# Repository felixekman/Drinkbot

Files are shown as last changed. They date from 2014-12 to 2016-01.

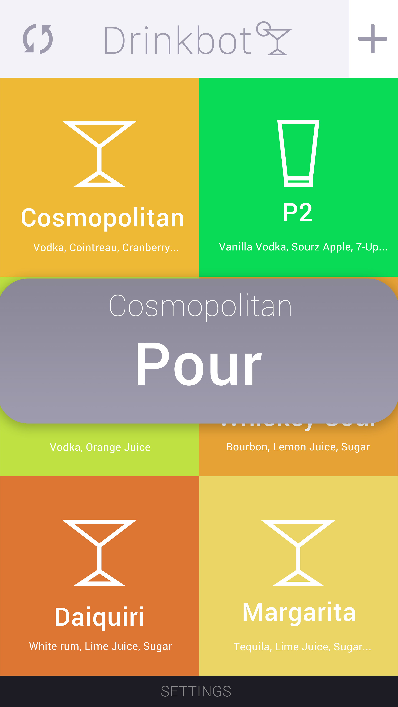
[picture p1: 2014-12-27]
AppDevelopment/AppGUI-Order.jpg

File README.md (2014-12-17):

Drinkbot
========

An attempt at controlling a bunch of peristaltic pumps

I have ordered 8 Peristaltic Pumps. 12VDC 200-300mA
  https://www.adafruit.com/products/1150

I hope to drive them via a Raspberry Pi Model B and a Spark core.
I want to be able to control the pumps individually with Mosfets for ON/OFF operation (Possibly via PWM) from the GPIO pins on the Raspberry Pi. I hope to connect the pumps via RJ45 connectors for easy connect and disconnect. I want to drive the entire system from a single 12V power supply.
My current plan is to build my own PCB (first time ever so I need a little help) using these components and ordering the PCB from OSHPark.

Components for the build:

1 pcs Raspberry Pi Model B

1 pcs Spark Core http://spark.io

8 pcs Peristaltic Pumps. 12VDC 200-300mA (https://www.adafruit.com/products/1150)

8 pcs RJ45 8-Pin connectors (https://www.sparkfun.com/products/643)

8 pcs N-Channel MOSFET 60V 30A FQP30N06L (https://www.sparkfun.com/products/10213)

8 pcs 10k Ohm 1/4th W Resistors (https://www.sparkfun.com/products/8374)

8 pcs 1N4007 Diode MIC DO-41 1A 1000V Rectifier Diode

1 pcs Voltage Regulator - 5V L7805 (https://www.sparkfun.com/products/107)

1 pcs Raspberry Pi - GPIO Shrouded Header (2x13)

This project is released under Open Source Hardware (OSHW) licence and the coming software is released under a OSI-approved open source license!

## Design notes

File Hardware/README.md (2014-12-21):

Drinkbot
========

Version 1 of Drinkbot Hardware
Schematics and Layout in Eagle CAD

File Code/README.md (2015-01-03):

Drinkbot
========

## State Machine
```
                   BOOTING
                      |
                      v
   (collect data) LISTENING <-+
        API called? Y |       |
                      v       |
                    START     |
                      |       | finished? Y
                      v       |
              +--> PUMPING    |
  finished? N |       |       |
              +-------+-------+
                      |
                      v
                     end (never reach here)
```

## APIs
```
[librae@centos build]$ spark list
Checking with the cloud...
Retrieving cores... (this might take a few seconds)
core-librae (111111111111111111111111) is online
  Variables:
    temperature (double)
    alcohol1 (double)
    alcohol2 (double)
  Functions:
    int setpumps(String args)
    int debug(String args)
```

### Variables
```
$ spark get DrinkbotPrototype temperature
1454
```
or
```
$ curl https://api.spark.io/v1/devices/111111111111111111111111/temperature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

{
  "cmd": "VarReturn",
  "name": "temperature",
  "result": 1446,
  "coreInfo": {
    "last_app": "",
    "last_heard": "2015-01-03T16:27:09.022Z",
    "connected": true,
    "deviceID": "111111111111111111111111"
  }
}
```

### Functions

```
$ spark call DrinkbotPrototype setpumps "P0:10;P1:00;P2:20;P3:05;P4:07;P5:15;P6:00;P7:10"
0
```
or
```
$ curl https://api.spark.io/v1/devices/111111111111111111111111/setpumps \
	-d access_token=ffffffffffffffffffffffffffffffffffffffff \
	-d "args=P0:03;P1:03;P2:10;P3:12;P4:01;P5:02;P6:04;P7:00"

{
  "id": "111111111111111111111111",
  "name": "core-librae",
  "last_app": null,
  "connected": true,
  "return_value": 0
}
```

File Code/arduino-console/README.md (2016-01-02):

# arduino-console
A simple portable console module for Arduino.<br>
Originally ported from Ousia console. http://ousia.accrete.org/

## Features
* Easy for adding new commands
* Arguments passing through
* Simply extendable

## Running Demo
```
console starts...
Please press ENTER to activate it.

$
$ ?
available commands:
	help
	?
	debug
```
```
$ who
who: command not found
```
```
$ debug param1 param2
argv[1]: param1
argv[2]: param2
argc: 3
cmd_debug
```
## TODO
It would help a lot if anyone can pack it to be an Arduino Library.

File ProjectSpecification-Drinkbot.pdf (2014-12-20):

Project

Specification:

Drinkbot
Custom

Hardware:

Drinkbot

(OSHW)
https://github.com/felixekman/Drinkbot Schematics

available

as

DrinkbotPCB.pdf

Main

Processing

Unit:

Spark

Core
Secondary

Processing

Unit:

ATmega328P

Important

information

for

System:

8

Pumps,

connected

to

pins

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
Spark

Core
Pumps

are

controlled

via

MOSFET’s

(FQP30N06L)

Alcohol

Sensor

(MQ3)

connected

to

pin

A2

on

Spark

Core
Temperature

Sensor

(DS18B20)

connected

to

pin

D4

on

Spark

Core

Secondary

Processing

Unit

controlled

via

Serial

from

Spark

Core.

TX/RX

Connected

on
TX/RX

pins

on

Spark

Core.

RGB

led

(Neopixel)

connected

to

Spark

Core

on

pin

D7.

Functions

and

control

sequences:

Commands

arrives

to

Spark

Core

via

Curl/Spark.function/Spark.variable

:Command

syntax:
For

Drink

order/Pump

order:

Ex:

P0:10;P1:00;P2:20;P3:05;P4:07;P5:15;P6:00;P7:10 Ex

2:

P0:XX;P1:XX;P2:XX;P3:XX;P4:XX;P5:XX;P6:XX;P7:XX

The

command

will

always

have

this

format

P0,P1

etc. corresponds

to

the

pump,

the
following

two

values

is

the

cl

value

that

the

specific

pump

should

produce.

This

cl

value
corresponds

to

a

specific

“on

time”

value

for

each

cl.

So

for

example

for

Pump

1,

P1:10,
i.e.

10

cl

would

equal

a

delay

of

500*10

=

5000.

This

is

to

be

set

by

variable

that

can

be
changed

via

Spark.function

call. When

command

is

finished

and

all

pumps

are

done

the
API

response

should

return

an

“All

done”,

if

any

error

occurs

during

the

run

this

should
also

be

returned.

For

information

on

this

please

refer

to:
http://docs.spark.io/firmware/ and http://docs.spark.io/api/

Also,

very

important!

Incoming

command

must

be

executed

in

"parallel",

I.e.

I

want

to
issue

a

curl

commands

that

trigger

all

the

pumps

to

run

for

a

set

time.

But

I

want

to

be
able

to

trigger

them

all

so

I

don’t

have

to

wait

for

each

pump

to

finish

before

continuing
to

the

next

one,

i.e.

not

a

cascading

run.

There

is

some

sample

code

available

for

this

in

this

file on

Github

(SampleCode.txt that
gives

some

pointers

on

how

we

want

it

to

be

done.

For

Alcohol

Sensor

order:

When

a

command

comes

in

from

the

Server

the

Spark

Core

should

turn

on

the

Alcohol
Sensor,

wait

[delay(6000)],

read

the

value

from

it

and

convert

it

to

BAC

and

return

it

in
the

response. This

is

done

by

simply

reading

the

analogRead(0) value

of

pin

A2

and then
calculating %

BAC

with

the

analogRead value

and

the

calculations

available here:
https://code.google.com/p/ece387breathalyzer/wiki/theCode

Example:

We

issue

a

Curl

order

on

a

Server

side

app

via

this

command:

curl
https://api.spark.io/v1/devices/0123456789abcdef01234567/alcohol?access_token=1 2341234123412341234123412

//

EXAMPLE

RESPONSE
{
"cmd":

"VarReturn",
"name":

"alcohol",
"result":

0.06,
"coreInfo":

{
"last_app":

"",
"last_heard":

"2014-‐08-‐22T22:33:25.407Z", "connected":

true,
"deviceID":

"53ff6c065075535119511687" }

Example:

On

Spark:

“Spark.variable("alcohol",

&alcohol,

INT);”

On

Spark

Core’s

side

it

simply

turns

on

the

alcohol

sensor,

waits

a

set

amount

of

time,
then

reads

the

value

from

the

alcohol

sensors

analog

voltage and response and
calculates the

estimated

BAC.

For

Temperature Sensor order:

Same

as

Alcohol

Sensor

order,

but

instead

reads

value

from

DS18B20 sensor

and
outputs

it

to

a

temperature variable

instead. The

library

for

the

DS18B20

is

available in
the

Spark

IDE

(SPARK-‐DALLAS-‐TEMPERATURE)

Sample

code

can

be

found

here:
http://www.reuk.co.uk/wordpress/ds18b20-‐temperature-‐measurement-‐with-‐spark-‐core/

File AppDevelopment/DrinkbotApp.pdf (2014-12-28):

Drinkbot

App

-‐ Proof

of

Concept

Development

Application

name:

Drinkbot
Type:

Open

Source

Distribution
Platform:

iOS

/

(Possibly

Android)

:For

iOS:
Language:

Preferably

Swift

code
Devices:

Universal

(for

both

iPad

and

iPhone)
Type:

Single-‐View

Application

Mockup

design

available

here:
https://github.com/felixekman/Drinkbot/tree/master/Graphics

Pour

orders

to

the

server

is

made

via

a

HTTP REST

Post

command

to

example

request:
curl

https://api.spark.io/v1/devices/0123456789abcdef01234567/order

\
-‐d

access_token=1234123412341234123412341234123412341234

\
-‐d

params=” P0:XX;P1:XX;P2:XX;P3:XX;P4:XX;P5:XX;P6:XX;P7:XX"

Where

0123456789abcdef01234567 for

example

is

the

UnitID,
1234123412341234123412341234123412341234

are for

example

the

AccessToken.

The

example

drink

database

is

hosted

with

Amazon

AWS

and

credentials

are

available

to
developers.

The

parameters

(params)

are

relevant

to

the

selected

drink

in

the

application.

When
selected

it

populates

the

fields

in

the

(params)

taken

from

the

corresponding

drink

in
the

DrinkTable

from

the

database.

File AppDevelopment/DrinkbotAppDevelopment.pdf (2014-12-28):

# Main Screen

# See: Scroll Example

Press goes to Settings Screen

Press goes to New Drink Screen

Press Icon always goes to Main Screen

Refreshes list: Cleans list and downloads from database

Image Populated from Database: Under DrinkTable -> URL
for each drink.
Image in URL is Always 2000x2000px scaled to fit screen.

# Main Screen

# Scroll Example

# Settings

Press Icon always goes to Main Screen (Not Saving)

This field sets the UnitID in the HTTP REST Post request that is used for the Pour order

This field sets the AccessToken in the HTTP REST Post request that is used for the Pour order

Saves Settings permanently for this App

This field sets the URL to where the MySQL database is hosted for the drink database

# New Drink

Press Icon always goes to Main Screen (Not Saving)

Saves Settings permanently for this App

This field is equivalent to the “Name” field in the DrinkTable
This field is equivalent to the “LiquorName” field in the LiquorTable. This is automatically populated for each field from the database.

This field is equivalent to part of the “Content0” field in the DrinkTable. This is relevant to the LiquorTable and DrinkTable and here the user can set the amount, which then is saved as a new drink with a new ID in the database.

# Order

Press Icon always goes to Main Screen (Cancel Pour/Order)

This field is equivalent to the DrinkName from the DrinkTable of the picture pressed.

When the word “Pour” is pressed a single HTTP REST Post is sent to the Server equivalent to the syntax for the Drink in the Table and for the API.

This pops up over the main meny when a drink is pressed. This goes away if the user presses outside of the “bubble”

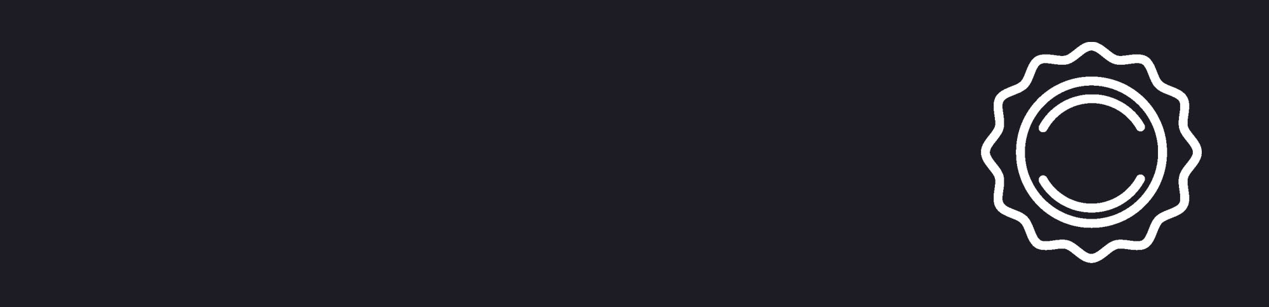
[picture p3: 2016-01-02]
Code/PhonegapApp/Online/www/img/settings.jpg

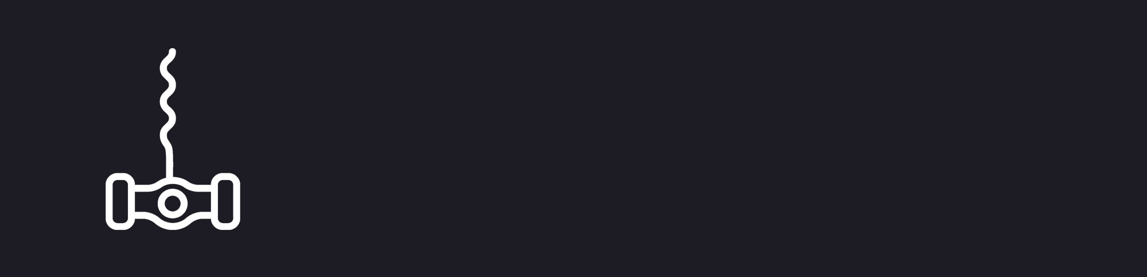
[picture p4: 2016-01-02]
Code/PhonegapApp/Online/www/img/corkscrew.jpg

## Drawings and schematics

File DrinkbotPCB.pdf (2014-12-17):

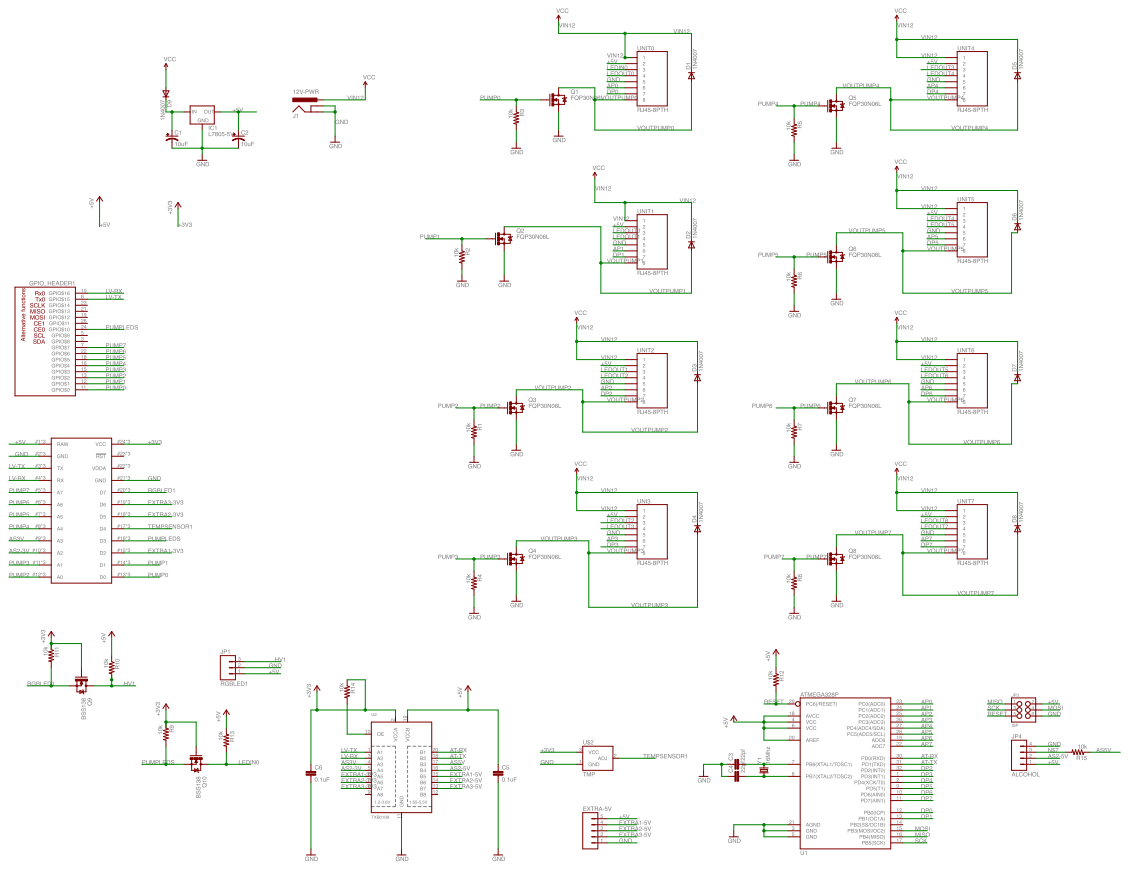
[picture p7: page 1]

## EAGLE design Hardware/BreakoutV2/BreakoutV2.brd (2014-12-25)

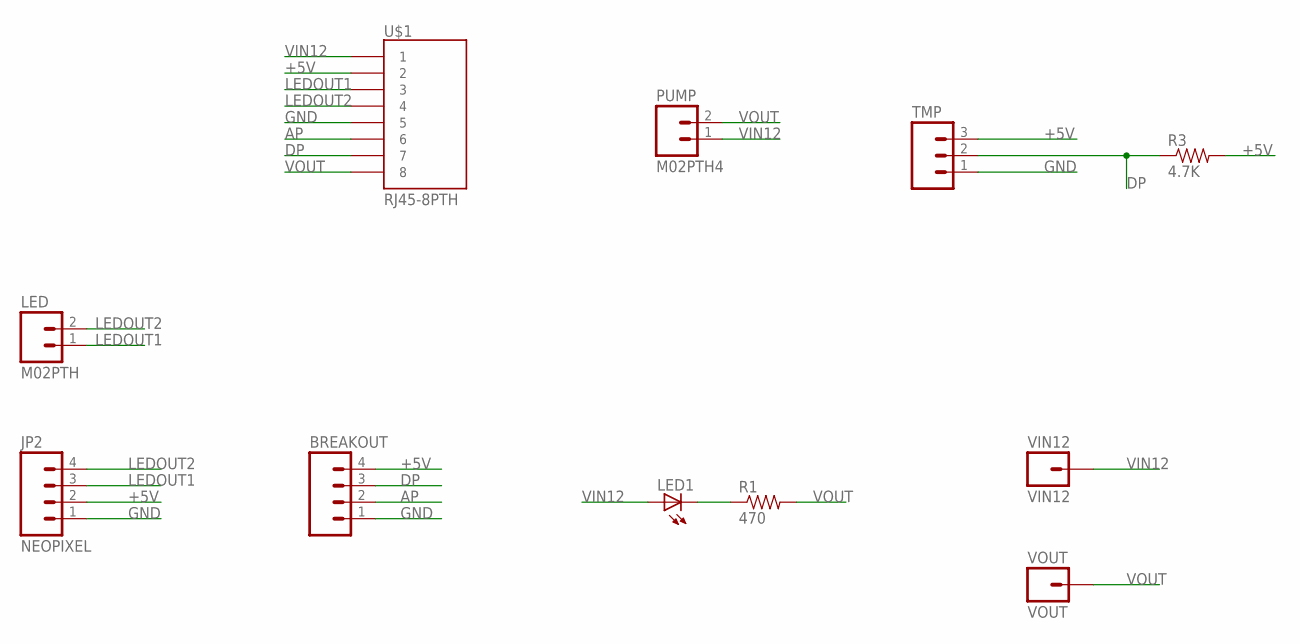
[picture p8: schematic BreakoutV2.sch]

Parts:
BREAKOUT: M04PTH; 1X04
JP2: NEOPIXEL; 1X04
LED: M02PTH; 1X02
LED1: LED5MM
PUMP: M02PTH4; 1X02_XTRA_BIG
R1: 470; 1/6W-RES
R3: 4.7K; 1/6W-RES
TMP: M03PTH; 1X03
U$1: RJ45-8PTH; RJ45-8
VIN12: VIN12; 1X01_POGOPIN_HOLE_0.58
VOUT: VOUT; 1X01_POGOPIN_HOLE_0.58

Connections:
+5V: BREAKOUT.4, JP2.2, R3.2, TMP.3, U$1.2
AP: BREAKOUT.2, U$1.6
DP: BREAKOUT.3, R3.1, TMP.2, U$1.7
GND: BREAKOUT.1, JP2.1, TMP.1, U$1.5
LEDOUT1: JP2.3, LED.1, U$1.3
LEDOUT2: JP2.4, LED.2, U$1.4
unnamed: LED1.K (C), R1.1
VIN12: LED1.A, PUMP.1, U$1.1, VIN12.1
VOUT: PUMP.2, R1.2, U$1.8, VOUT.1

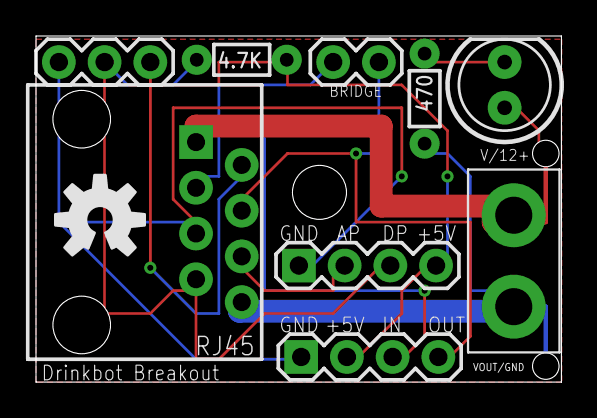
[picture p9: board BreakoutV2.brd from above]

Board: 2 copper layers, 29.2 x 19.2 mm, 12 parts (0 on the bottom side), 9 nets.

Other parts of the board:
U$2: OSHW-LOGO-M

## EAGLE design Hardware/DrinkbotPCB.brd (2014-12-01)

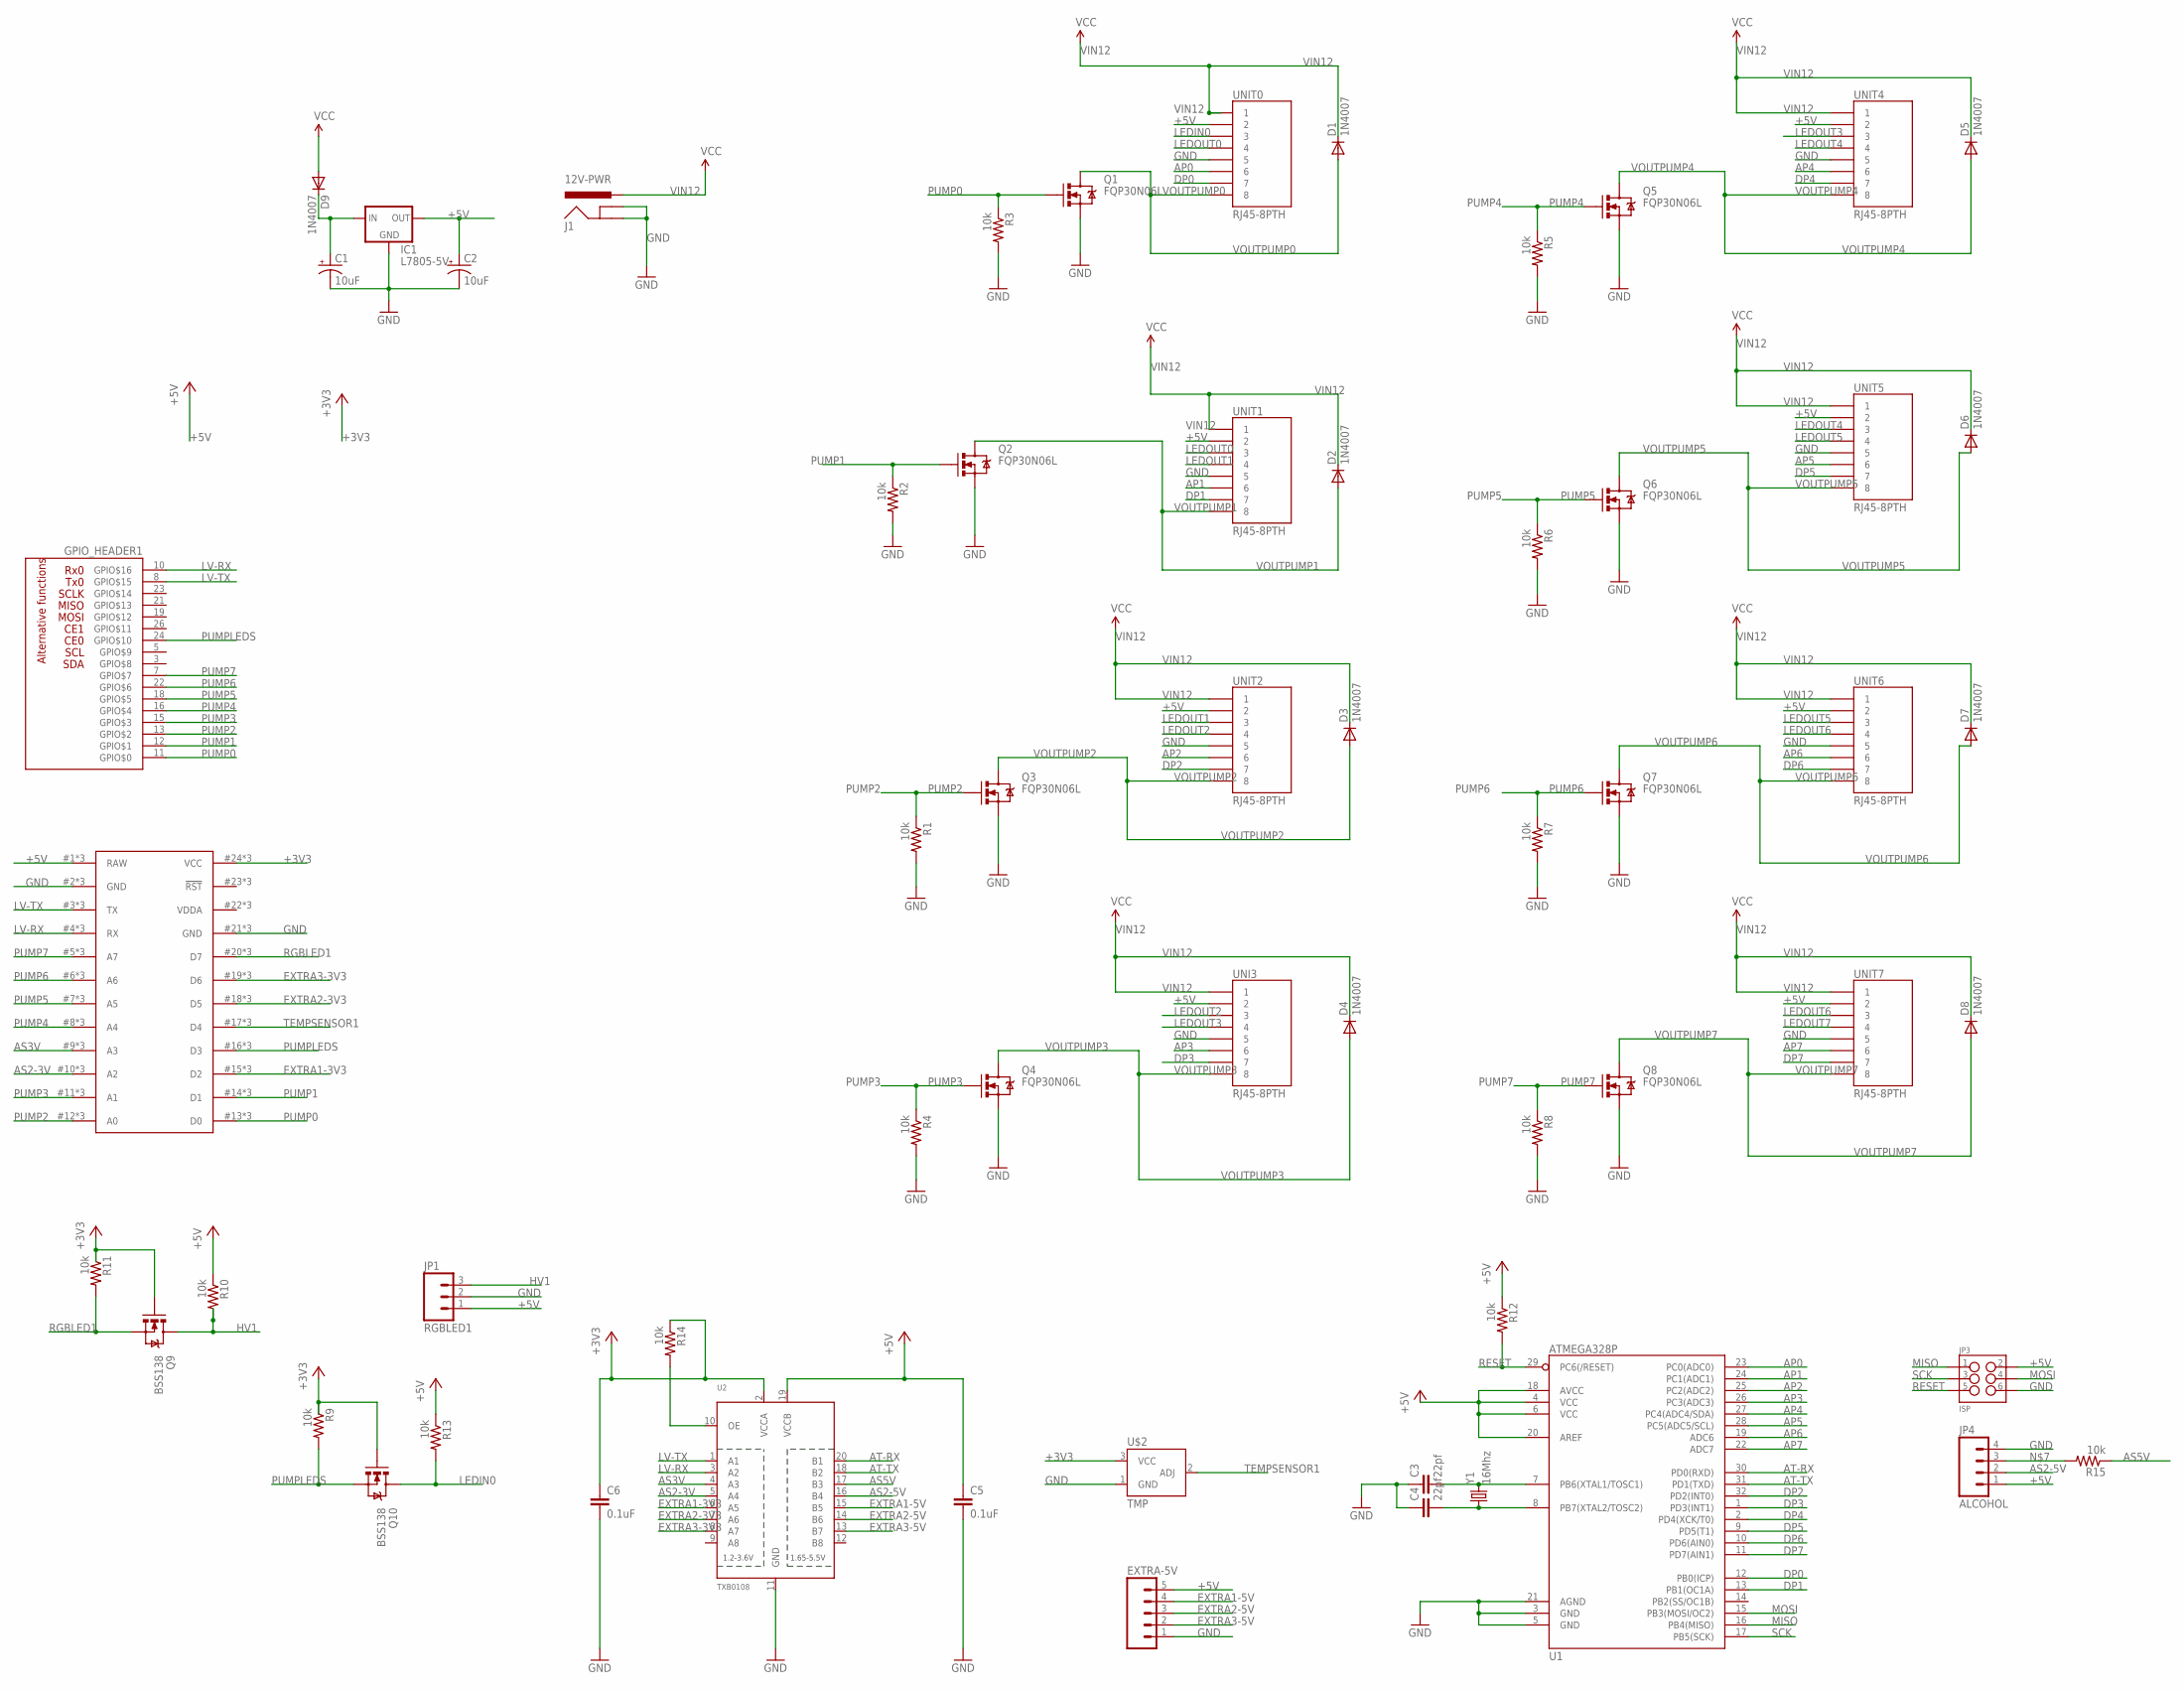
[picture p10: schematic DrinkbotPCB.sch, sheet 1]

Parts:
C1, C2: 10uF; CPOL-RADIAL-10UF-25V
C3, C4: 22pf; CAP-PTH-SMALL-KIT
C5, C6: 0.1uF; CAP-PTH-SMALL-KIT
D1, D2, D3, D4, D5, D6, D7, D8, D9: 1N4007; DIODE-1N4001
EXTRA-5V: M05PTH; 1X05
GPIO_HEADER1: RPI-GPIO; 2X13
IC1: L7805-5V; TO220-IGO
J1: 12V-PWR; POWER_JACK_PTH
JP1: RGBLED1; JST-3-PTH
JP3: ISP; 2X3-SHROUDED
JP4: ALCOHOL; 1X04
Q1, Q2, Q3, Q4, Q5, Q6, Q7, Q8: FQP30N06L; TO220V
Q9, Q10: BSS138; SOT23
R1, R2, R3, R4, R5, R6, R7, R8, R9, R10, R11, R12, R13, R14, R15: 10k; 1/6W-RES
U1: ATMEGA328P; TQFP32-08
U2: TXB0108; TSSOP20
U$1: SPARK-CORE; SPARK_CORE_STACKABLE
U$2: TMP; TO-92
UNI3: RJ45-8PTH; RJ45-8
UNIT0, UNIT1, UNIT2, UNIT4, UNIT5, UNIT6, UNIT7: RJ45-8PTH; RJ45-8
Y1: 16Mhz; HC49US

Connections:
+3V3: C6.1, GPIO_HEADER1.1 (+3V3), GPIO_HEADER1.17 (+3V3), Q9.1 (G), Q10.1 (G), R9.1, R11.1, R14.1, U2.2 (VCCA), U$1.24 (VCC), U$1.#24 (VCC), U$1.@24 (VCC), U$2.3 (VCC)
+5V: C2.1 (+), C5.1, EXTRA-5V.5, GPIO_HEADER1.2 (+5V), GPIO_HEADER1.4 (+5V), IC1.OUT, JP1.1, JP3.2, JP4.1, R10.1, R12.1, R13.1, U1.4 (VCC), U1.6 (VCC), U1.18 (AVCC), U1.20 (AREF), U2.19 (VCCB), U$1.1 (RAW), U$1.#1 (RAW), U$1.@1 (RAW), UNI3.2, UNIT0.2, UNIT1.2, UNIT2.2, UNIT4.2, UNIT5.2, UNIT6.2, UNIT7.2
AP0: U1.23 (PC0(ADC0)), UNIT0.6
AP1: U1.24 (PC1(ADC1)), UNIT1.6
AP2: U1.25 (PC2(ADC2)), UNIT2.6
AP3: U1.26 (PC3(ADC3)), UNI3.6
AP4: U1.27 (PC4(ADC4/SDA)), UNIT4.6
AP5: U1.28 (PC5(ADC5/SCL)), UNIT5.6
AP6: U1.19 (ADC6), UNIT6.6
AP7: U1.22 (ADC7), UNIT7.6
AS2-3V: U2.5 (A4), U$1.10 (A2), U$1.#10 (A2), U$1.@10 (A2)
AS2-5V: JP4.2, U2.16 (B4)
AS3V: U2.4 (A3), U$1.9 (A3), U$1.#9 (A3), U$1.@9 (A3)
AS5V: R15.1, U2.17 (B3)
AT-RX: U1.30 (PD0(RXD)), U2.20 (B1)
AT-TX: U1.31 (PD1(TXD)), U2.18 (B2)
DP0: U1.12 (PB0(ICP)), UNIT0.7
DP1: U1.13 (PB1(OC1A)), UNIT1.7
DP2: U1.32 (PD2(INT0)), UNIT2.7
DP3: U1.1 (PD3(INT1)), UNI3.7
DP4: U1.2 (PD4(XCK/T0)), UNIT4.7
DP5: U1.9 (PD5(T1)), UNIT5.7
DP6: U1.10 (PD6(AIN0)), UNIT6.7
DP7: U1.11 (PD7(AIN1)), UNIT7.7
EXTRA1-3V3: U2.6 (A5), U$1.15 (D2), U$1.#15 (D2), U$1.@15 (D2)
EXTRA1-5V: EXTRA-5V.4, U2.15 (B5)
EXTRA2-3V3: U2.7 (A6), U$1.18 (D5), U$1.#18 (D5), U$1.@18 (D5)
EXTRA2-5V: EXTRA-5V.3, U2.14 (B6)
EXTRA3-3V3: U2.8 (A7), U$1.19 (D6), U$1.#19 (D6), U$1.@19 (D6)
EXTRA3-5V: EXTRA-5V.2, U2.13 (B7)
GND: C1.2 (-), C2.2 (-), C3.1, C4.1, C5.2, C6.2, EXTRA-5V.1, GPIO_HEADER1.6 (GND), GPIO_HEADER1.9 (GND), GPIO_HEADER1.14 (GND), GPIO_HEADER1.20 (GND), GPIO_HEADER1.25 (GND), IC1.GND, J1.GND, J1.GNDBREAK, JP1.2, JP3.6, JP4.4, Q1.3 (S), Q2.3 (S), Q3.3 (S), Q4.3 (S), Q5.3 (S), Q6.3 (S), Q7.3 (S), Q8.3 (S), R1.2, R2.2, R3.2, R4.2, R5.2, R6.2, R7.2, R8.2, U1.3 (GND), U1.5 (GND), U1.21 (AGND), U2.11 (GND), U$1.2 (GND), U$1.21 (GND), U$1.#2 (GND), U$1.#21 (GND), U$1.@2 (GND), U$1.@21 (GND), U$2.1 (GND), UNI3.5, UNIT0.5, UNIT1.5, UNIT2.5, UNIT4.5, UNIT5.5, UNIT6.5, UNIT7.5
HV1: JP1.3, Q9.3 (D), R10.2
LEDIN0: Q10.3 (D), R13.2, UNIT0.3
LEDOUT0: UNIT0.4, UNIT1.3
LEDOUT1: UNIT1.4, UNIT2.3
LEDOUT2: UNI3.3, UNIT2.4
LEDOUT3: UNI3.4, UNIT4.3
LEDOUT4: UNIT4.4, UNIT5.3
LEDOUT5: UNIT5.4, UNIT6.3
LEDOUT6: UNIT6.4, UNIT7.3
LEDOUT7: UNIT7.4
LV-RX: GPIO_HEADER1.10 (GPIO$16), U2.3 (A2), U$1.4 (RX), U$1.#4 (RX), U$1.@4 (RX)
LV-TX: GPIO_HEADER1.8 (GPIO$15), U2.1 (A1), U$1.3 (TX), U$1.#3 (TX), U$1.@3 (TX)
MISO: JP3.1, U1.16 (PB4(MISO))
MOSI: JP3.4, U1.15 (PB3(MOSI/OC2))
unnamed: C1.1 (+), D9.C, IC1.IN
unnamed: C3.2, U1.7 (PB6(XTAL1/TOSC1)), Y1.2
unnamed: C4.2, U1.8 (PB7(XTAL2/TOSC2)), Y1.1
unnamed: R14.2, U2.10 (OE)
unnamed: JP4.3, R15.2
PUMP0: GPIO_HEADER1.11 (GPIO$0), Q1.1 (G), R3.1, U$1.13 (D0), U$1.#13 (D0), U$1.@13 (D0)
PUMP1: GPIO_HEADER1.12 (GPIO$1), Q2.1 (G), R2.1, U$1.14 (D1), U$1.#14 (D1), U$1.@14 (D1)
PUMP2: GPIO_HEADER1.13 (GPIO$2), Q3.1 (G), R1.1, U$1.12 (A0), U$1.#12 (A0), U$1.@12 (A0)
PUMP3: GPIO_HEADER1.15 (GPIO$3), Q4.1 (G), R4.1, U$1.11 (A1), U$1.#11 (A1), U$1.@11 (A1)
PUMP4: GPIO_HEADER1.16 (GPIO$4), Q5.1 (G), R5.1, U$1.8 (A4), U$1.#8 (A4), U$1.@8 (A4)
PUMP5: GPIO_HEADER1.18 (GPIO$5), Q6.1 (G), R6.1, U$1.7 (A5), U$1.#7 (A5), U$1.@7 (A5)
PUMP6: GPIO_HEADER1.22 (GPIO$6), Q7.1 (G), R7.1, U$1.6 (A6), U$1.#6 (A6), U$1.@6 (A6)
PUMP7: GPIO_HEADER1.7 (GPIO$7), Q8.1 (G), R8.1, U$1.5 (A7), U$1.#5 (A7), U$1.@5 (A7)
PUMPLEDS: GPIO_HEADER1.24 (GPIO$10), Q10.2 (S), R9.2, U$1.16 (D3), U$1.#16 (D3), U$1.@16 (D3)
RESET: JP3.5, R12.2, U1.29 (PC6(/RESET))
RGBLED1: Q9.2 (S), R11.2, U$1.20 (D7), U$1.#20 (D7), U$1.@20 (D7)
SCK: JP3.3, U1.17 (PB5(SCK))
TEMPSENSOR1: U$1.17 (D4), U$1.#17 (D4), U$1.@17 (D4), U$2.2 (ADJ)
VDDA: U$1.22 (VDDA), U$1.#22 (VDDA), U$1.@22 (VDDA)
VIN12: D1.C, D2.C, D3.C, D4.C, D5.C, D6.C, D7.C, D8.C, D9.A, J1.PWR, UNI3.1, UNIT0.1, UNIT1.1, UNIT2.1, UNIT4.1, UNIT5.1, UNIT6.1, UNIT7.1
VOUTPUMP0: D1.A, Q1.2 (D), UNIT0.8
VOUTPUMP1: D2.A, Q2.2 (D), UNIT1.8
VOUTPUMP2: D3.A, Q3.2 (D), UNIT2.8
VOUTPUMP3: D4.A, Q4.2 (D), UNI3.8
VOUTPUMP4: D5.A, Q5.2 (D), UNIT4.8
VOUTPUMP5: D6.A, Q6.2 (D), UNIT5.8
VOUTPUMP6: D7.A, Q7.2 (D), UNIT6.8
VOUTPUMP7: D8.A, Q8.2 (D), UNIT7.8

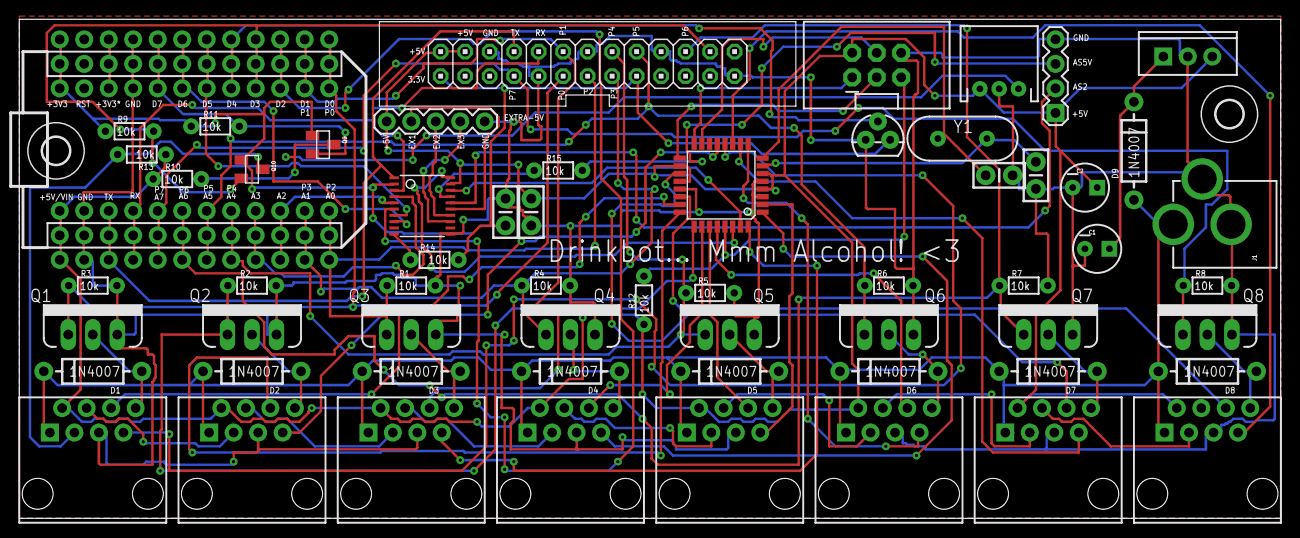
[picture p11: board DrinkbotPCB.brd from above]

Board: 2 copper layers, 130.8 x 51.7 mm, 62 parts (0 on the bottom side), 72 nets.

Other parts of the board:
U$3, U$7: 2,8

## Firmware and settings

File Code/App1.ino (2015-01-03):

// This #include statement was automatically added by the Spark IDE.
/**
 ******************************************************************************
 * @file    application.cpp
 * @authors  Satish Nair, Zachary Crockett and Mohit Bhoite
 * @version V1.0.0
 * @date    05-November-2013
 * @brief   Tinker application
 ******************************************************************************
  Copyright (c) 2013 Spark Labs, Inc.  All rights reserved.

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
  You should have received a copy of the GNU Lesser General Public
  License along with this program; if not, see <http://www.gnu.org/licenses/>.
 ******************************************************************************
 */

/*
 * Brief of Drinkbot
 *
 * State Machine:
 *
 *                   BOOTING
 *                      |
 *                      v
 *   (collect data) LISTENING <-+
 *        API called? Y |       |
 *                      v       |
 *                    START     |
 *                      |       | finished? Y
 *                      v       |
 *              +--> PUMPING    |
 *  finished? N |       |       |
 *              +-------+-------+
 *                      |
 *                      v
 *                     end (never reach here)
 */

/* Includes ------------------------------------------------------------------*/
#include "application.h"
#include "neopixel/neopixel.h" //Neopixel RGBLED

/* Definitions ---------------------------------------------------------------*/
SYSTEM_MODE(AUTOMATIC);

enum {
	STATE_BOOTING = 0,
	STATE_LISTENING = 1,
	STATE_START = 2,
	STATE_PUMPING = 3,
	STATE_MAX,
};

#define NPUMPS		8
#define vol2time(vol)	((unsigned long)vol*1000)	// vol -> millis, to be fixed according to actual case

//Neopixel RGBLED
#define PIXEL_PIN D7
#define PIXEL_COUNT 24
#define PIXEL_TYPE WS2812B
Adafruit_NeoPixel strip = Adafruit_NeoPixel(PIXEL_COUNT, PIXEL_PIN, PIXEL_TYPE);

/* Variables -----------------------------------------------------------------*/
static double temperature = 0.0;
static double alcohol1 = 0.0;
static double alcohol2 = 0.0;
static int state = STATE_BOOTING;
static int pumpsOnVol[NPUMPS] = {0, 0, 0, 0, 0, 0, 0, 0};	// unit: cl
static int pumpsStatus[NPUMPS] = {0, 0, 0, 0, 0, 0, 0, 0};	// 1: on, 0: off
static unsigned long timeStart = 0;

static const int pump2io[NPUMPS] = {D0, D1, A0, A1, A4, A5, A6, A7};

/* Function prototypes -------------------------------------------------------*/
int tinkerDigitalRead(String pin);
int tinkerDigitalWrite(String command);
int tinkerAnalogRead(String pin);
int tinkerAnalogWrite(String command);
int drinkbotSetPumps(String command);
int drinkbotDebug(String command);

static void changestate(int s);
static int parseparams(String command, int id);
static int collectdata(void);
static void controlpump(int id, boolean on);
static void startpumpjobs(int p[NPUMPS]);
static int npumpson(int ps[NPUMPS]);
static void finishpumpjobs(int p[NPUMPS]);

/* This function is called once at start up ----------------------------------*/
void setup()
{
	int i;

	//Setup the logging functions
	Serial.begin(9600);

	//Setup communication bus with secondary processor
//	Serial1.begin(9600);

	//Setup the Tinker application here
	RGB.brightness(12);
	
	//Neopixel RGBLED
	strip.begin();
	strip.show(); // Initialize all pixels to 'off'

	//Register all the Tinker functions
//	Spark.function("digitalread", tinkerDigitalRead);
//	Spark.function("digitalwrite", tinkerDigitalWrite);

//	Spark.function("analogread", tinkerAnalogRead);
//	Spark.function("analogwrite", tinkerAnalogWrite);

	//Register all the Drinkbot functions
	Spark.function("setpumps", drinkbotSetPumps);
	Spark.function("debug", drinkbotDebug);

	//Register all the Drinkbot variables
	Spark.variable("temperature", &temperature, DOUBLE);
	pinMode(D4, INPUT);
	Spark.variable("alcohol1", &alcohol1, DOUBLE);
	pinMode(A3, INPUT);
	Spark.variable("alcohol2", &alcohol2, DOUBLE);
	pinMode(A2, INPUT);

	//Pumps
	for (i = 0; i < NPUMPS; i++) {
		pinMode(pump2io[i], OUTPUT);
		digitalWrite(pump2io[i], LOW);
	}

	//RGB LED
	pinMode(D7, OUTPUT);
}

/* This function loops forever --------------------------------------------*/
void loop()
{
	switch (state) {
	case STATE_BOOTING:
		Serial.println("Booting...");

		temperature = 0.0;
		alcohol1 = 0.0;
		alcohol2 = 0.0;
		state = STATE_BOOTING;
		memset(pumpsOnVol, 0, sizeof(pumpsOnVol));
		memset(pumpsStatus, 0, sizeof(pumpsStatus));
		timeStart = 0;

		changestate(STATE_LISTENING);
		break;
	case STATE_LISTENING:
		/*
		 * sleep here awaiting for remote api calls,
		 * or collect data from sensors
		 */
		collectdata();
		break;
	case STATE_START:
		startpumpjobs(pumpsOnVol);
		changestate(STATE_PUMPING);
		break;
	case STATE_PUMPING:
		finishpumpjobs(pumpsOnVol);
		break;
	default:
		Serial.print("no such state: ");
		Serial.println(state);
		break;
	}
}

/*******************************************************************************
 * Function Name  : tinkerDigitalRead
 * Description    : Reads the digital value of a given pin
 * Input          : Pin
 * Output         : None.
 * Return         : Value of the pin (0 or 1) in INT type
                    Returns a negative number on failure
 *******************************************************************************/
int tinkerDigitalRead(String pin)
{
	//convert ascii to integer
	int pinNumber = pin.charAt(1) - '0';
	//Sanity check to see if the pin numbers are within limits
	if (pinNumber < 0 || pinNumber > 7)
		return -1;

	if(pin.startsWith("D"))
	{
		pinMode(pinNumber, INPUT_PULLDOWN);
		return digitalRead(pinNumber);
	}
	else if (pin.startsWith("A"))
	{
		pinMode(pinNumber + 10, INPUT_PULLDOWN);
		return digitalRead(pinNumber + 10);
	}
	return -2;
}

/*******************************************************************************
 * Function Name  : tinkerDigitalWrite
 * Description    : Sets the specified pin HIGH or LOW
 * Input          : Pin and value
 * Output         : None.
 * Return         : 1 on success and a negative number on failure
 *******************************************************************************/
int tinkerDigitalWrite(String command)
{
	bool value = 0;
	//convert ascii to integer
	int pinNumber = command.charAt(1) - '0';
	//Sanity check to see if the pin numbers are within limits
	if (pinNumber < 0 || pinNumber > 7) return -1;

	if(command.substring(3, 7) == "HIGH") value = 1;
	else if(command.substring(3, 6) == "LOW") value = 0;
	else return -2;

	if(command.startsWith("D"))
	{
		pinMode(pinNumber, OUTPUT);
		digitalWrite(pinNumber, value);
		return 1;
	}
	else if(command.startsWith("A"))
	{
		pinMode(pinNumber + 10, OUTPUT);
		digitalWrite(pinNumber + 10, value);
		return 1;
	}
	else return -3;
}

/*******************************************************************************
 * Function Name  : tinkerAnalogRead
 * Description    : Reads the analog value of a pin
 * Input          : Pin
 * Output         : None.
 * Return         : Returns the analog value in INT type (0 to 4095)
                    Returns a negative number on failure
 *******************************************************************************/
int tinkerAnalogRead(String pin)
{
	//convert ascii to integer
	int pinNumber = pin.charAt(1) - '0';
	//Sanity check to see if the pin numbers are within limits
	if (pinNumber < 0 || pinNumber > 7) return -1;

	if(pin.startsWith("D"))
	{
		pinMode(pinNumber, INPUT);
		return analogRead(pinNumber);
	}
	else if (pin.startsWith("A"))
	{
		pinMode(pinNumber + 10, INPUT);
		return analogRead(pinNumber + 10);
	}
	return -2;
}

/*******************************************************************************
 * Function Name  : tinkerAnalogWrite
 * Description    : Writes an analog value (PWM) to the specified pin
 * Input          : Pin and Value (0 to 255)
 * Output         : None.
 * Return         : 1 on success and a negative number on failure
 *******************************************************************************/
int tinkerAnalogWrite(String command)
{
	//convert ascii to integer
	int pinNumber = command.charAt(1) - '0';
	//Sanity check to see if the pin numbers are within limits
	if (pinNumber < 0 || pinNumber > 7) return -1;

	String value = command.substring(3);

	if(command.startsWith("D"))
	{
		pinMode(pinNumber, OUTPUT);
		analogWrite(pinNumber, value.toInt());
		return 1;
	}
	else if(command.startsWith("A"))
	{
		pinMode(pinNumber + 10, OUTPUT);
		analogWrite(pinNumber + 10, value.toInt());
		return 1;
	}
	else return -2;
}

/*******************************************************************************
 * Function Name  : drinkbotSetPumps
 * Description    : Setup and start the pumping jobs,
 *                  e.g. P0:xx;P1:xx;P2:xx;P3:xx;P4:xx;P5:xx;P6:xx;P7:xx
 *                  where P0 ~ P7 are the 8 pumps and xx is the cl value.
 * Input          : pumps id and corresponding cl value string
 * Output         : None.
 * Return         : 0 for success, others for error numbers
 *******************************************************************************/
int drinkbotSetPumps(String command)
{
	int i;

	Serial.print(__func__);
	Serial.print(", args: ");
	Serial.println(command);

	if (command.length() != 47) {
//		Serial.println("Please use correct format for args, e.g.");
//		Serial.println("\tP0:10;P1:00;P2:20;P3:05;P4:07;P5:15;P6:00;P7:10");
		return -EINVAL;
	}

	if (state != STATE_LISTENING) {
		return -EBUSY;
	}

	/* parse command */
	Serial.print("pumpsOnVol: ");
	for (i = 0; i < NPUMPS; i++) {
		pumpsOnVol[i] = parseparams(command, i);
		Serial.print(pumpsOnVol[i]);
		Serial.print(' ');
	}
	Serial.println("");

	changestate(STATE_START);
	return 0;
}

/*******************************************************************************
 * Function Name  : drinkbotDebug
 * Description    : Debugging purpose
 * Input          : Random things
 * Output         : None
 * Return         : The character ascii code it received
 *******************************************************************************/
int drinkbotDebug(String command)
{
	int i;

	Serial.print(__func__);
	Serial.print(", args: ");
	Serial.println(command);

	if (command.equals("reset")) {
		Serial.println("Resetting Drinkbot...");
		for (i = 0; i < NPUMPS; i++)
			controlpump(i, false);
		changestate(STATE_BOOTING);
	}


	Serial.println("dump all variables:");

	Serial.print("temperature: ");
	Serial.println(temperature);

	Serial.print("alcohol1: ");
	Serial.println(alcohol1);

	Serial.print("alcohol2: ");
	Serial.println(alcohol2);

	Serial.print("state: ");
	Serial.println(state);

	Serial.print("timeStart: ");
	Serial.println(timeStart);

	Serial.print("pumpsOnVol: ");
	for (i = 0; i < NPUMPS; i++) {
		Serial.print(pumpsOnVol[i]);
		Serial.print(' ');
	}
	Serial.println("");

	Serial.print("pumpsStatus: ");
	for (i = 0; i < NPUMPS; i++) {
		Serial.print(pumpsStatus[i]);
		Serial.print(' ');
	}
	Serial.println("");

	return command.charAt(0);
}


static void changestate(int s)
{
	if (s < 0 || s >= STATE_MAX)
		Serial.print("change state failed: ");
	else
		Serial.print("change state: ");
	Serial.print(state);
	Serial.print(" -> ");
	Serial.println(s);
	state = s;
}

// the parameters should follow below format:
//     P0:XX;P1:XX;P2:XX;P3:XX;P4:XX;P5:XX;P6:XX;P7:XX
static int parseparams(String command, int id)
{
	return command.substring(6*id+3, 6*id+5).toInt();
}

// TODO need to poll sensors and calculate data
static int collectdata(void)
{
	int reading = 0;

	reading = analogRead(A3);
	alcohol1 = reading;
	reading = analogRead(A2);
	alcohol2 = reading;
	reading = analogRead(D4);
	temperature = reading;

	return 0;
}

static void controlpump(int id, boolean on)
{
	if (id < 0 || id > NPUMPS) {
		Serial.print("invalid pump id: ");
		Serial.println(id);
		id = constrain(id, 0, (NPUMPS-1));
	}

	pinMode(pump2io[id], OUTPUT);
	if (on) {
		digitalWrite(pump2io[id], HIGH);
		pumpsStatus[id] = 1;
	} else {
		digitalWrite(pump2io[id], LOW);
		pumpsStatus[id] = 0;
	}
}

static void startpumpjobs(int p[NPUMPS])
{
	int i;

	timeStart = millis();
	Serial.print("timeStart: ");
	Serial.println(timeStart);

	Serial.print("starting pumps: ");
	for (i = 0; i < NPUMPS; i++) {
		if (p[i] != 0) {
			controlpump(i, true);
			Serial.print(i);
			Serial.print(' ');
		}
	}
	Serial.println("");
}

static int npumpson(int ps[NPUMPS])
{
	int i, n = 0;
	for (i = 0; i < NPUMPS; i++)
		n += ps[i];
	return n;
}

static void finishpumpjobs(int p[NPUMPS])
{
	int i;
	unsigned long timeDelta;

	// FIXME
	// support up to about 49 days for an unsigned long millis
	// better to wrap around
	timeDelta = millis() - timeStart;

	for (i = 0; i < NPUMPS; i++) {
		if (timeDelta > vol2time(p[i]) &&
		    pumpsStatus[i] == 1) {
			Serial.print("stoping pump: ");
			Serial.print(i);
			Serial.print(" in ");
			Serial.print(timeDelta);
			Serial.println("ms");
			controlpump(i, false);
		}
	}

	if (npumpson(pumpsStatus) == 0) {
		Serial.print("All pumping jobs finished, time elapsed: ");
		Serial.println(timeDelta);
		changestate(STATE_LISTENING);
	}
}

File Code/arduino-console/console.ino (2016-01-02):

#include <stddef.h>
#include <stdarg.h>
#include "list.h"
#include "console.h"

#define MAX_ARGV_ENTRIES	4

typedef int (*cmd_fn_type)(int argc, char **argv);
struct cmd_handle {
	char *cmd_word;
	cmd_fn_type cmd_fn;
};

static struct console_cmd concmd;
static char *argv[MAX_ARGV_ENTRIES];
static int argc;

static int cmd_help(int argc, char **argv);
static int cmd_debug(int argc, char **argv);

const struct cmd_handle hcmd_arr[] = {
	{
		"help",
		cmd_help,
	},
	{
		"?",
		cmd_help,
	},
	{
		"debug",
		cmd_debug,
	},
	{
		NULL,
		NULL,
	}
};

static void os_printf(char *fmt, ... )
{
	char buf[128];
	va_list args;
	va_start(args, fmt );
	vsnprintf(buf, 128, fmt, args);
	va_end(args);
	Serial.print(buf);
}

void commands_register(struct console_cmd *conc)
{
	conc->hcmd_arr = hcmd_arr;
}

static int cmd_help(int argc, char **argv)
{
	const struct cmd_handle *c;
	os_printf("available commands:\n\r");
	for (c = &hcmd_arr[0]; c->cmd_word != NULL; c++)
		os_printf("\t%s\n\r", c->cmd_word);
	return 0;
}

static int cmd_debug(int argc, char **argv)
{
	os_printf("%s\n\r", __func__);
	return 0;
}


static void __cmd_char_push(struct console_cmd *conc, char ch)
{
	struct cmd_char *cc;

	if (conc->ccs.nc >= 0 && conc->ccs.nc < CMD_CHAR_BUF_SIZE) {
		cc = &conc->cbuf[conc->ccs.nc];
		cc->c = ch;
		list_add(&cc->list, &conc->ccs.s);
		conc->ccs.nc++;
	}
	conc->ccs.nc_tot++;
}

static void __cmd_char_pop(struct console_cmd *conc)
{
	struct cmd_char *cc;

	if (conc->ccs.nc_tot > conc->ccs.nc) {
		conc->ccs.nc_tot--;
		return;
	}
	if (conc->ccs.nc > 0 && conc->ccs.nc <= CMD_CHAR_BUF_SIZE) {
		cc = &conc->cbuf[conc->ccs.nc - 1];
		cc->c = 0;
		list_del(&cc->list);
		conc->ccs.nc--;
	}
	if (conc->ccs.nc_tot > 0)
		conc->ccs.nc_tot--;
}

static void __cmd_char_stack_flush(struct console_cmd *conc)
{
	struct cmd_char *cc, *cc_tmp;
	list_for_each_entry_safe(cc, cc_tmp, &conc->ccs.s, list) {
		list_del(&cc->list);
		cc->c = 0;
	}
	conc->ccs.nc = 0;
	conc->ccs.nc_tot = 0;
	memset(conc->cbuf, 0, sizeof(conc->cbuf));
}

static int parse_cmd(struct console_cmd *conc)
{
	char str[32] = { 0 };
	char *args = NULL;
	char *tok = NULL;
	static char *cmd_saveptr = NULL;
	int i;

	for (i = 0; i < conc->ccs.nc; i++)
		str[i] = conc->cbuf[i].c;

	tok = strtok_r(str, " ", &cmd_saveptr);

	for (i = 0; conc->hcmd_arr[i].cmd_word != NULL; i++) {
		if (strcmp(tok, conc->hcmd_arr[i].cmd_word) == 0) {
			conc->index = i;
			break;
		}
	}
	if (conc->index < 0) {
		os_printf("%s: command not found\n\r", tok);
		return 0;
	}

	memset(argv, 0, MAX_ARGV_ENTRIES * sizeof(char *));
	argv[0] = conc->hcmd_arr[conc->index].cmd_word;

	args = strtok_r(NULL, "\r", &cmd_saveptr);

	memset(conc->args, 0, CMD_CHAR_BUF_SIZE);
	i = 0;
	if (args != NULL) {
		strcpy(conc->args, args);
		cmd_saveptr = NULL;
		tok = strtok_r((char *)conc->args, " ", &cmd_saveptr);
		while (tok != NULL) {
			os_printf("argv[%d]: %s\n\r", ++i, tok);
			argv[i] = tok;
			if (i == MAX_ARGV_ENTRIES - 1)
				break;
			tok = strtok_r(NULL, " ", &cmd_saveptr);
		}
	}
	argc = i + 1;
	if (argc > 1)
		os_printf("argc: %d\n\r", argc);

	return strchr(args, '&') == NULL ? 0 : 1;
}

#ifdef DEBUG_CONSOLE
static int process_enter(struct console_cmd *conc)
{
	struct cmd_char *cc;
	list_for_each_entry_reverse(cc, &conc->ccs.s, list) {
		os_printf("%c", cc->c);
	}
	os_printf("\n\rnc: %d, tot: %d\n\r", conc->ccs.nc, conc->ccs.nc_tot);
	__cmd_char_stack_flush(conc);
	os_printf("$ ");
	return 0;
}
#else
static int process_enter(struct console_cmd *conc)
{
	int backend = 0;
	int ret;

	conc->index = -1;
	if (conc->ccs.nc > 0)
		backend = parse_cmd(conc);

	if (conc->index < 0)
		goto finish_enter;

	ret = conc->hcmd_arr[conc->index].cmd_fn(argc, argv);

	/* TODO Distinguish different kinds of errors per ret value */
	if (ret < 0) {
		os_printf("%s: exec failed %d\n\r",
				conc->hcmd_arr[conc->index].cmd_word, ret);
	}

finish_enter:
	__cmd_char_stack_flush(conc);
	Serial.print("$ ");

	return 0;
}
#endif /* DEBUG_CONSOLE */


void setup() {
	Serial.begin(9600);
	memset(&concmd, 0, sizeof(struct console_cmd));
	INIT_LIST_HEAD(&concmd.ccs.s);
	commands_register(&concmd);
	Serial.println("\n\rconsole starts...");
	Serial.println("Please press ENTER to activate it.");
}

void loop() {
	struct console_cmd *conc = &concmd;
	while (Serial.available()) {
		char ch = (char)Serial.read();
		switch (ch) {
		case '\r':
			Serial.print('\n');
			Serial.print('\r');
			process_enter(conc);
			break;
		case '\b':
			if (conc->ccs.nc != 0) {
				Serial.print('\b');
				Serial.print(' ');
				Serial.print('\b');
				__cmd_char_pop(conc);
			}
			break;
		default:
			Serial.print(ch);
			__cmd_char_push(conc, ch);
			break;
		}
	}
	delay(10);
}

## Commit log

2014-11-29 Initial upload of PCB/Schematics
    [DrinkbotPCB.brd, DrinkbotPCB.sch]
2014-11-29 PDF Schematics
2014-12-01 Updated Schematics/Gerbers/Board Layout
    [DrinkbotPCB.brd, DrinkbotPCB.sch]
2014-12-20 FlowChart added
2014-12-25 Added Breakout Board
    [BreakoutV2.brd, BreakoutV2.sch]
2014-12-27 New Logo & Rev. 2 for Drink Icons
    Reason: Calle…
2014-12-28 Sample Database
    [Drinkbot databas modell.xlsx]
2015-01-04 Updated RGB Strip Support
    The code now shows on rub led strip which pump is active. Also when
    pumping is done, an animation is shown to signal the drink is ready.
    [App-Dev.ino]
2015-01-09 Updated Code
    Updated code curtesy of Librae8226
    Also new RGB Led code from Felix
    1. refine code, remove unused code
    2. support dallas temperature sensor (onewire)
    3. support mq3 alcohol sensor
    4. work around virtual com port hang issue
    [App-DevAlt.ino]
2015-01-11 Supports customize each pump for its performance
    Use the const array millisPerVol[] to store the fixed parameter.
    Also, add a syslog macro for a better debugging purpose.
    Changes made by Librae8226
    [App.ino]
2016-01-02 Updated Structure
    [Drinkbot databas modell.xlsx]

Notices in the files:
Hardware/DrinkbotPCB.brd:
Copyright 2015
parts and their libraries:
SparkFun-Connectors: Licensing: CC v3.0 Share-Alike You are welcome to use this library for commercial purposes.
